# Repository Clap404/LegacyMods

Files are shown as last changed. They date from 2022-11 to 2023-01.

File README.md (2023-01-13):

# Clap404's Legacy Mods

This repo contains the mods I made for my custom [Voron Legacy](https://vorondesign.com/voron_legacy).
It's mainly made from the remains of an anet AM8 and a sidewinder X1 for the electronics, which is why its dimensions are :
- build volume : 200 x 300 x 270
- frame size : 380 x 480 x 440

## Basement Electronics Enclosure

This mod allows you to mount the eletronices on two 8mm rods (lead screws, smooth rods, threaded M8 rod, etc.) at the bottom of your printer, below the heated bed.
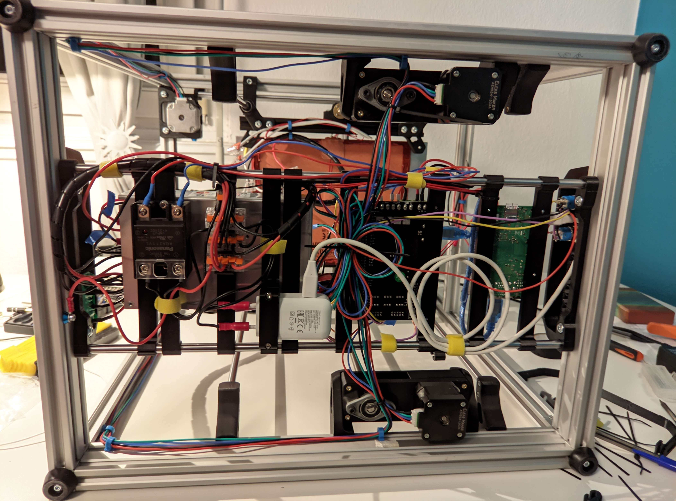
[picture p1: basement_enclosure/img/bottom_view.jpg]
bottom view

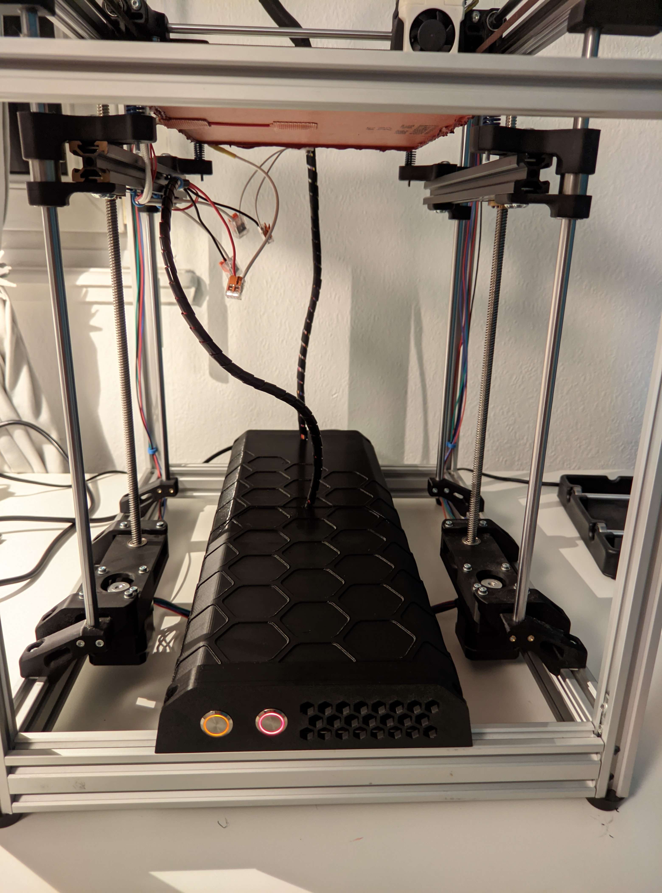
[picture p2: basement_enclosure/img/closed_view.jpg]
closed view


### Note

- You **will** have to edit the CAD to make this work for you.
- My printer is way longer (on the Y axis) than stock, so you may not be able to fit eveything if yours is shorter.
- I attached some components under the supporting rods, which brings the total height required to fit everything to 90mm. I have to raise the printer 10mm because i'm using 2040 extrusions, you'll need to raise it 30mm if you use 2020 extrusions, but you can choose to only attach things on top of the rods, using only 60mm.

### BOM

| description | quantity	| sourcing (non affiliate) 	|
|---|---|---|
| 8 mm rods of some kind	| 2		| your spare part bin / local hardware store |
| M5x16 BHCS screw		| 4		| same as voron's		|
| M5 post install T-nut		| 4		| same as voron's		|
| 16mm round push button	| 2		| [Aliexpress](https://fr.aliexpress.com/item/4001291695467.html)	|
| C14 fused socket w/ two poles switch	| 1	| [Aliexpress](https://fr.aliexpress.com/item/32706948395.html)		|
| 5x4 heat set inserts (for SSR)| 2		| same as voron's		|
| m3 screws (for mainboard)	| 4		| same as voron's 		|
| m2 plastic screws (for raspberry)	| 4	| same as voron's		|

## Z motor pulley box 

This mod is inspired by the v0.0 lead screw mechanism. It uses two pulleys and a loop belt to transfer the motion from the motor to the screw

### Features

- same width as a standard nema17 motor
- 1:2 reduction in the default configuration (provides no real benefit)
- avoids using a coupler, ensuring the lead screw is straight
- saves z-travel compared to using a coupler

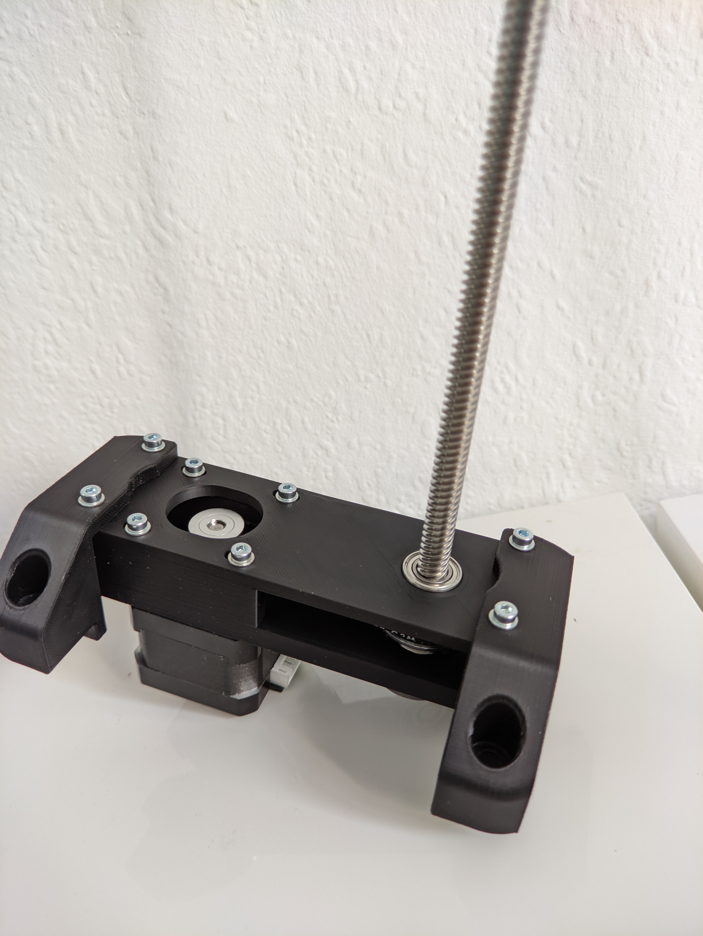
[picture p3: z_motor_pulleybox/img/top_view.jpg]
top view

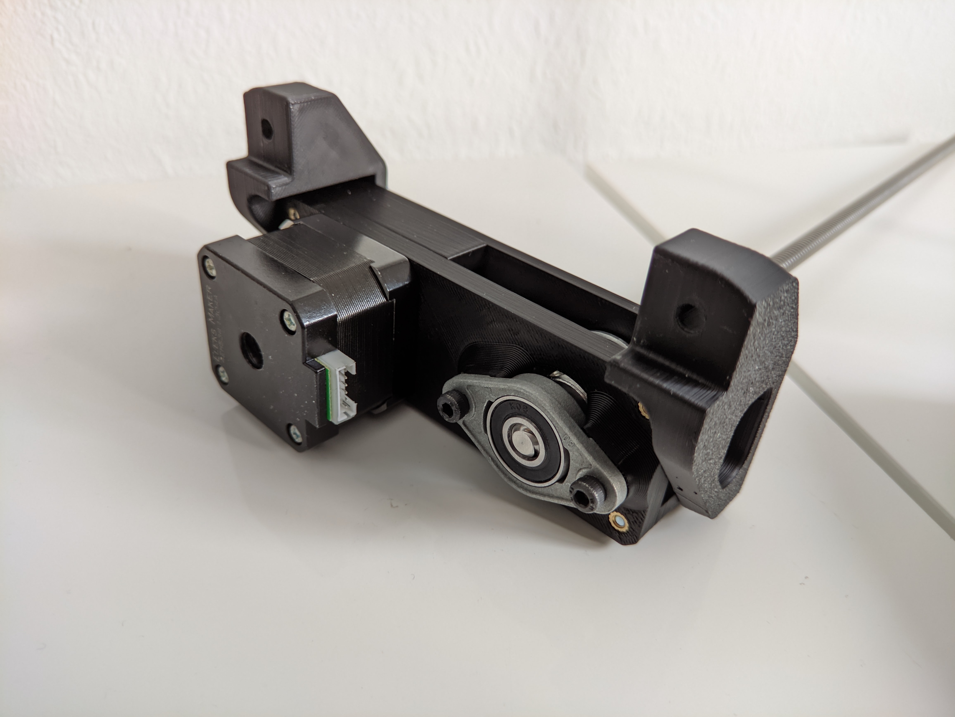
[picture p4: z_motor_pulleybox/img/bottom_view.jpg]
bottom view


### Note

- It should be possible to add 2 more holes around the lead screw hole, to be able to mount the pulleybox sideways.
- There is play in the KFL08 mounting holes to allow you to align the top and bottom bearings. After final assembly, if your lead screw is not straight, you can untighten the KFL08, reposition your lead screw and tighten it again.
- KFL08 bearings can have M4 or M5 holes for mounting... This model assumes you'll use M4 screws + nut to mount your KFL08 bearing but you should be able to enlarge the hole and nut pocket in CAD to accomodate for M5 hardware.
- I marked the F688-ZZ as optional because the pulleybox *should* work without it and allows a greater degree of movementof the lead screw, which might be desirable sometimes.

### BOM

this is the bom per pulley box (you probably neet 2)

| description | quantity	 | comment |
|---|---|---|
| m4x20 screw		 | 2		 | longer screws will work here too |
| m4 hex nut		 | 2		 | |
| m3x30 screw		 | 8		 | |
| m3x5 heat set inserts		 | 4		 | same as voron's |
| KFL08 bearing		 | 1		 | |
| GT2 belt loop 188mm | 1		 | same as voron's |
| 20t GT2 pulley 5mm bore | 1		 | same as voron's |
| 40t GT2 pulley 8mm bore | 1		 | not used in vorons ! |
| (optional) F688-ZZ | 1		 | found in some cheap printers |
| (optional) m3 washers		 | 8		 | bolting directly tends to deform the plastic |

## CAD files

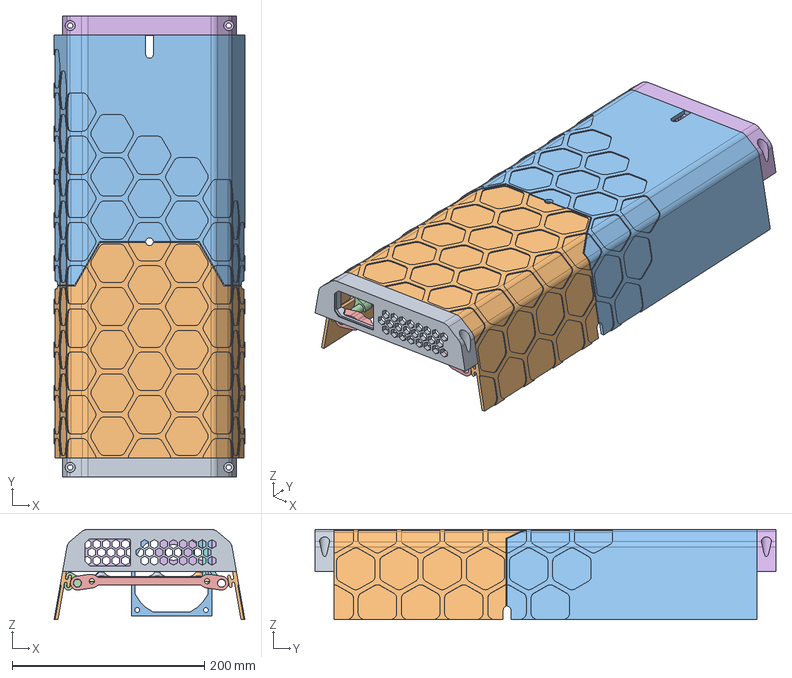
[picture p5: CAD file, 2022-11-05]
basement_enclosure/src/cover_large v8.step
198.7 x 480.0 x 94.0 mm
back-end
cover
cover_clip
rail_support
front_cover v5
bracket_ssr v3
bracket_psu v6
bracket_pi v4
base_bracket v2
Composant13
bracket_fan_80 v9

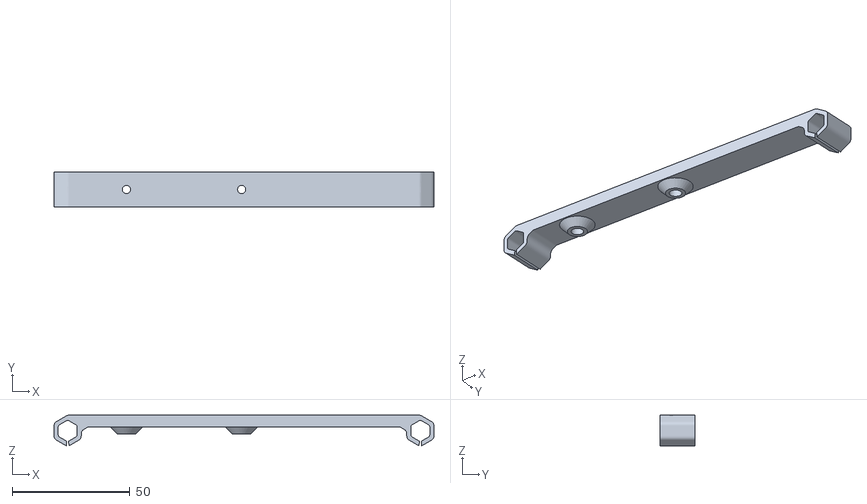
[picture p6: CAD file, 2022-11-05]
basement_enclosure/stl/bracket_ssr.stl
161.6 x 15.0 x 13.1

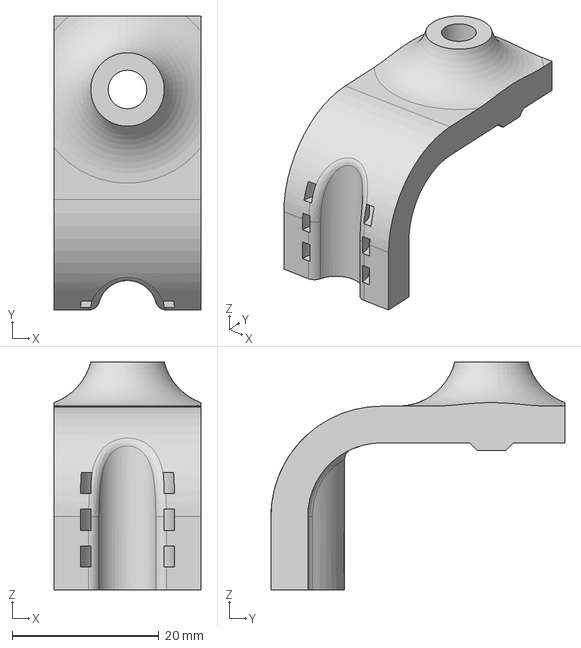
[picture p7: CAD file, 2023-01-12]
umbilical_support/umbilical_support v3.step
20.0 x 40.0 x 31.0 mm

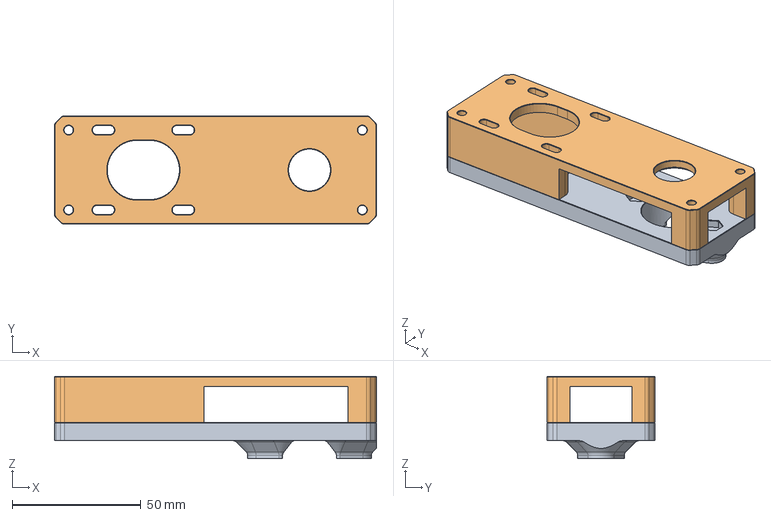
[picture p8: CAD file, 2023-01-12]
z_motor_pulleybox/motor pulley box v8.step
125.0 x 42.0 x 32.0 mm

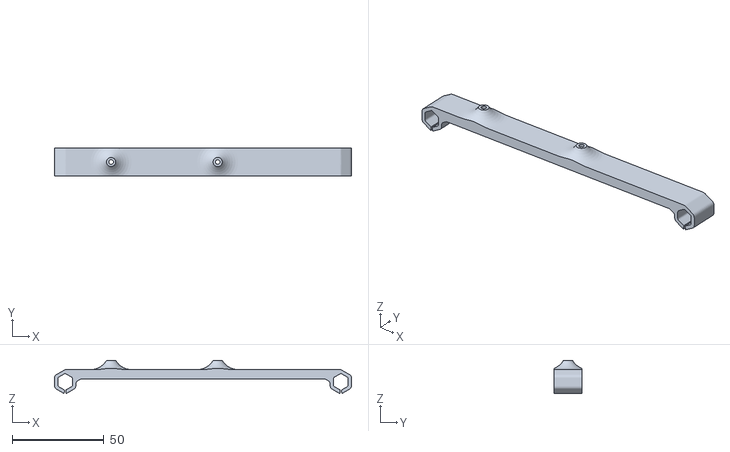
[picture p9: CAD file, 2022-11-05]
basement_enclosure/stl/bracket_pi.stl
161.6 x 15.0 x 18.1

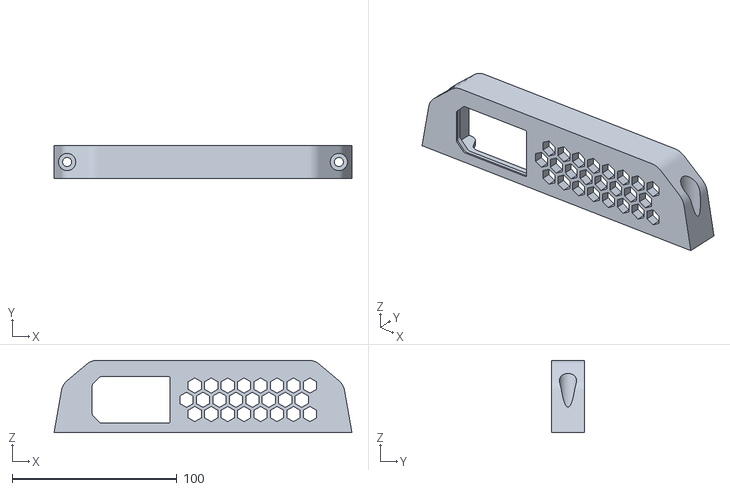
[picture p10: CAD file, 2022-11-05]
basement_enclosure/stl/back-end.stl
181.1 x 20.0 x 44.0

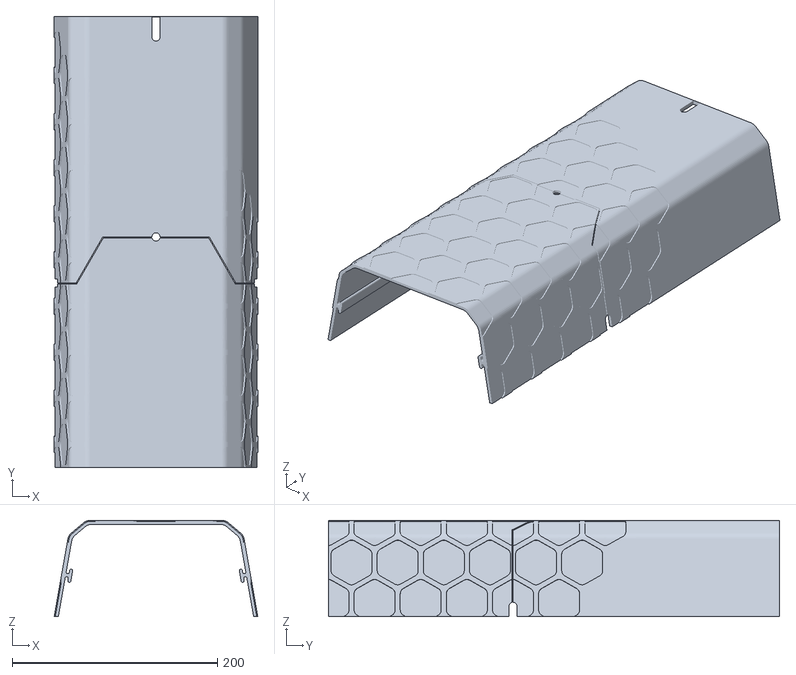
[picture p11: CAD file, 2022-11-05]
basement_enclosure/stl/cover.stl
198.7 x 440.0 x 94.0

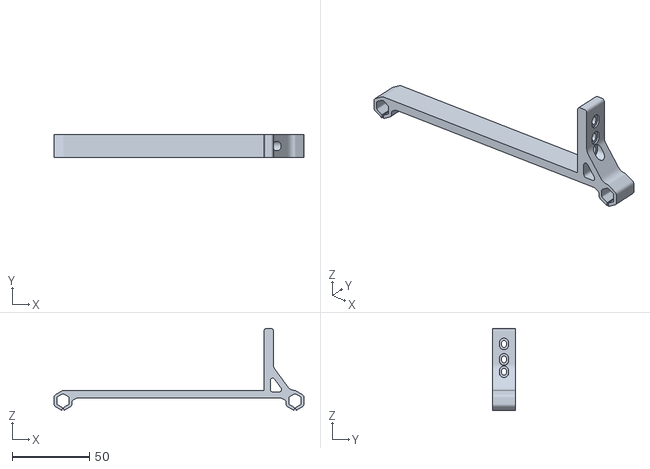
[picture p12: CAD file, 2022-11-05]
basement_enclosure/stl/rail_support.stl
161.6 x 15.0 x 53.1

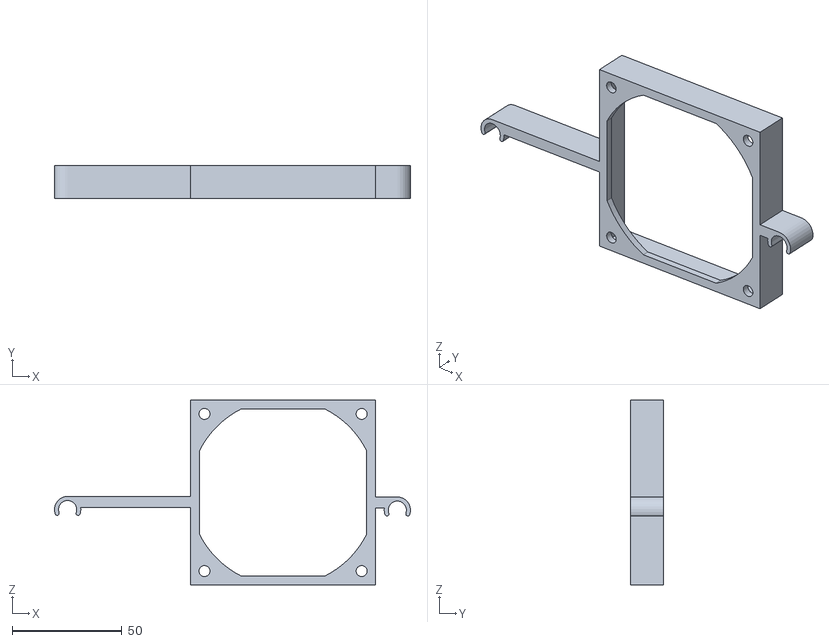
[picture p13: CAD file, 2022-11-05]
basement_enclosure/stl/fan_clip.stl
162.0 x 15.0 x 84.0

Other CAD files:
basement_enclosure/stl/bracket_mks.stl
umbilical_support/umbilical_support v3.3mf
umbilical_support/umbilical_support v3.f3d
z_motor_pulleybox/motor pulley box v8.3mf
z_motor_pulleybox/motor pulley box v8.f3d

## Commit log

2023-01-12 add pulley box
    [motor pulley box v8.3mf, motor pulley box v8.f3d, motor pulley box v8.step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]
2023-01-12 Add missing pièces to bom
2023-01-13 fix mistakes un bom
2023-01-13 add missing items to BOM and more precision
